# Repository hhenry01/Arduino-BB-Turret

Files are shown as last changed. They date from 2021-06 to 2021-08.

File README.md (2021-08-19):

# Arduino-BB-Turret
## About
The BB Turret is a project developed for [Zen Maker Lab](https://www.zenmakerlab.com/).

The code found under [BB_Turret](https://github.com/hhenry01/Arduino-BB-Turret/blob/main/BB_Turret/BB_Turret.ino) controls the shooting and aiming functions of the turret.

## How it Works
Full details surrounding the project belong to Zen Maker Lab. This README only describes the code and the circuit.
### Shooting

When a button is pressed, the Arduino outputs two voltages to the L298N module in order to spin a motor. One of the input pins is set to *HIGH* while the other is set to *LOW*. For more information, see an [L298N schematic](https://www.handsontec.com/dataspecs/L298N%20Motor%20Driver.pdf).\
\
The motor spins a gear in a rack and pinion system. The gear pushes the rack against a spring. The gear does not have teeth around its entire circumference, so the rack is eventually released and is propelled forward by a spring, hitting and shooting a projectile.

### Aiming
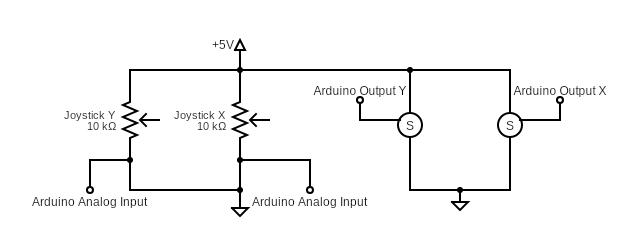
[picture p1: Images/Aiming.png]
Aiming Circuit


To aim the turret, a joystick controls the two servo motors. Since servos need specific angles, inputs must be processed. Smooth motion is created by taking the input and resizing it within an acceptable range for speed. Within that range lies different degrees of speed, simulating analog output, which is more intuitive and allows for finer control.\
\
The button in a joystick is not used because a dedicated button is preferable to control the DC motor. Using the joystick button makes it difficult to keep steady and hard to press when holding a direction. With a dedicated button, one can comfortably shoot the turret no matter the situation.\
\
Finally, at the end of the loop, a 10 ms delay is necessary. Without it, any input via the analog stick would cause immediately rotate the servos to their limits.

#### Full Circuit Schematic and Board
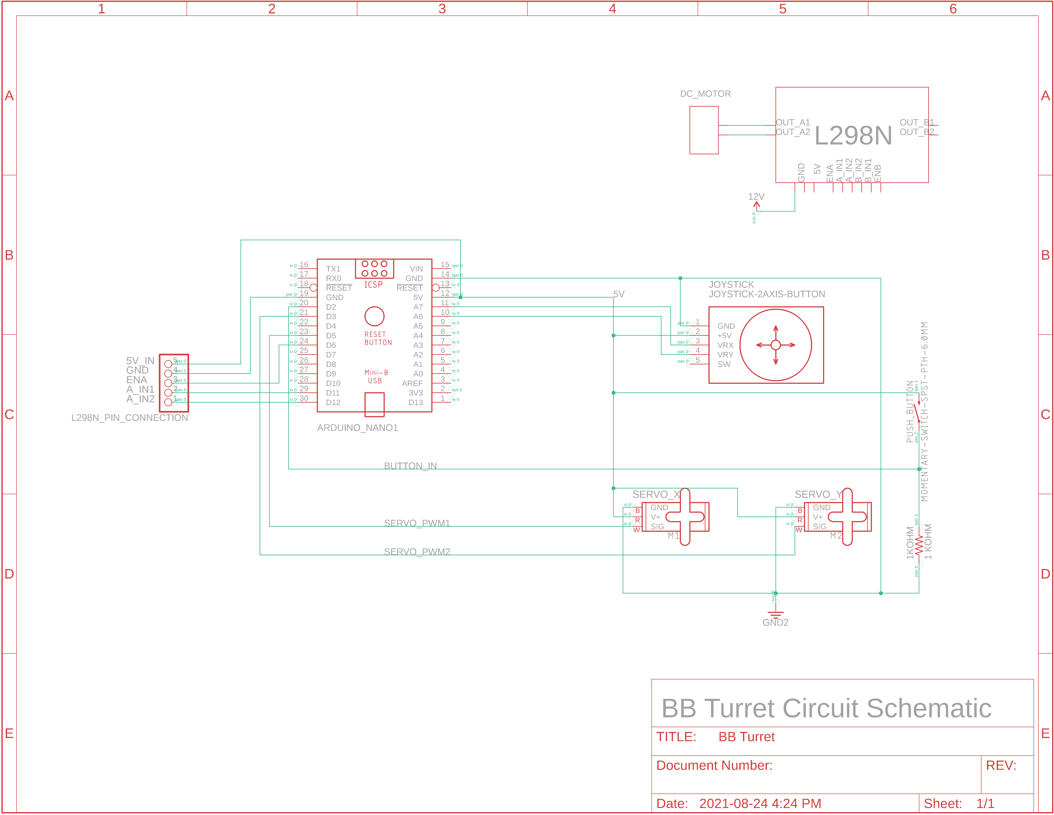
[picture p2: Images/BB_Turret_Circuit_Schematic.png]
Circuit Schematic
\
\
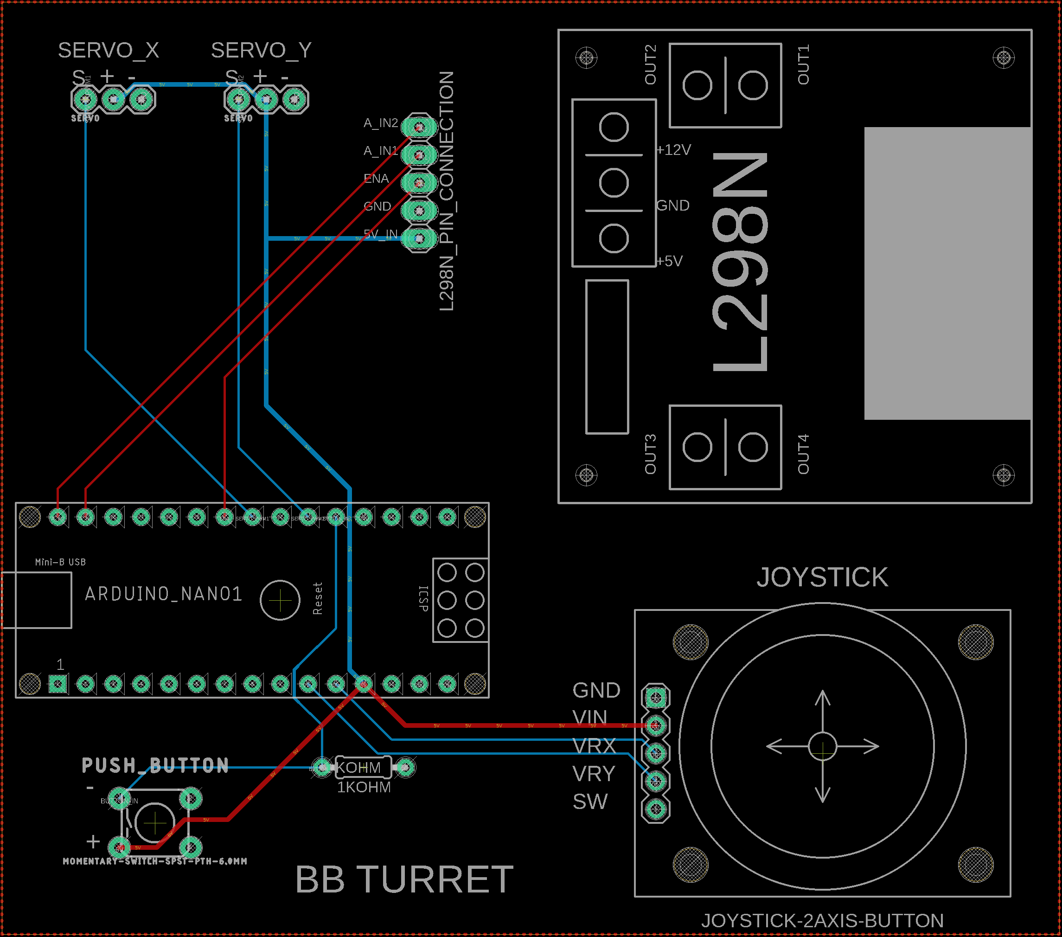
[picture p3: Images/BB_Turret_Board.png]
Board PCB
\
The PCB has a ground plane that connects all ground pins to each other.

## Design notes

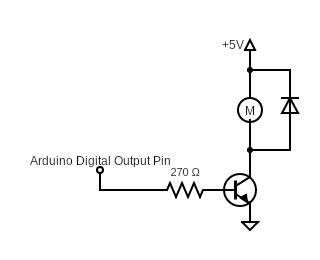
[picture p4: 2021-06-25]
Images/Motor.png

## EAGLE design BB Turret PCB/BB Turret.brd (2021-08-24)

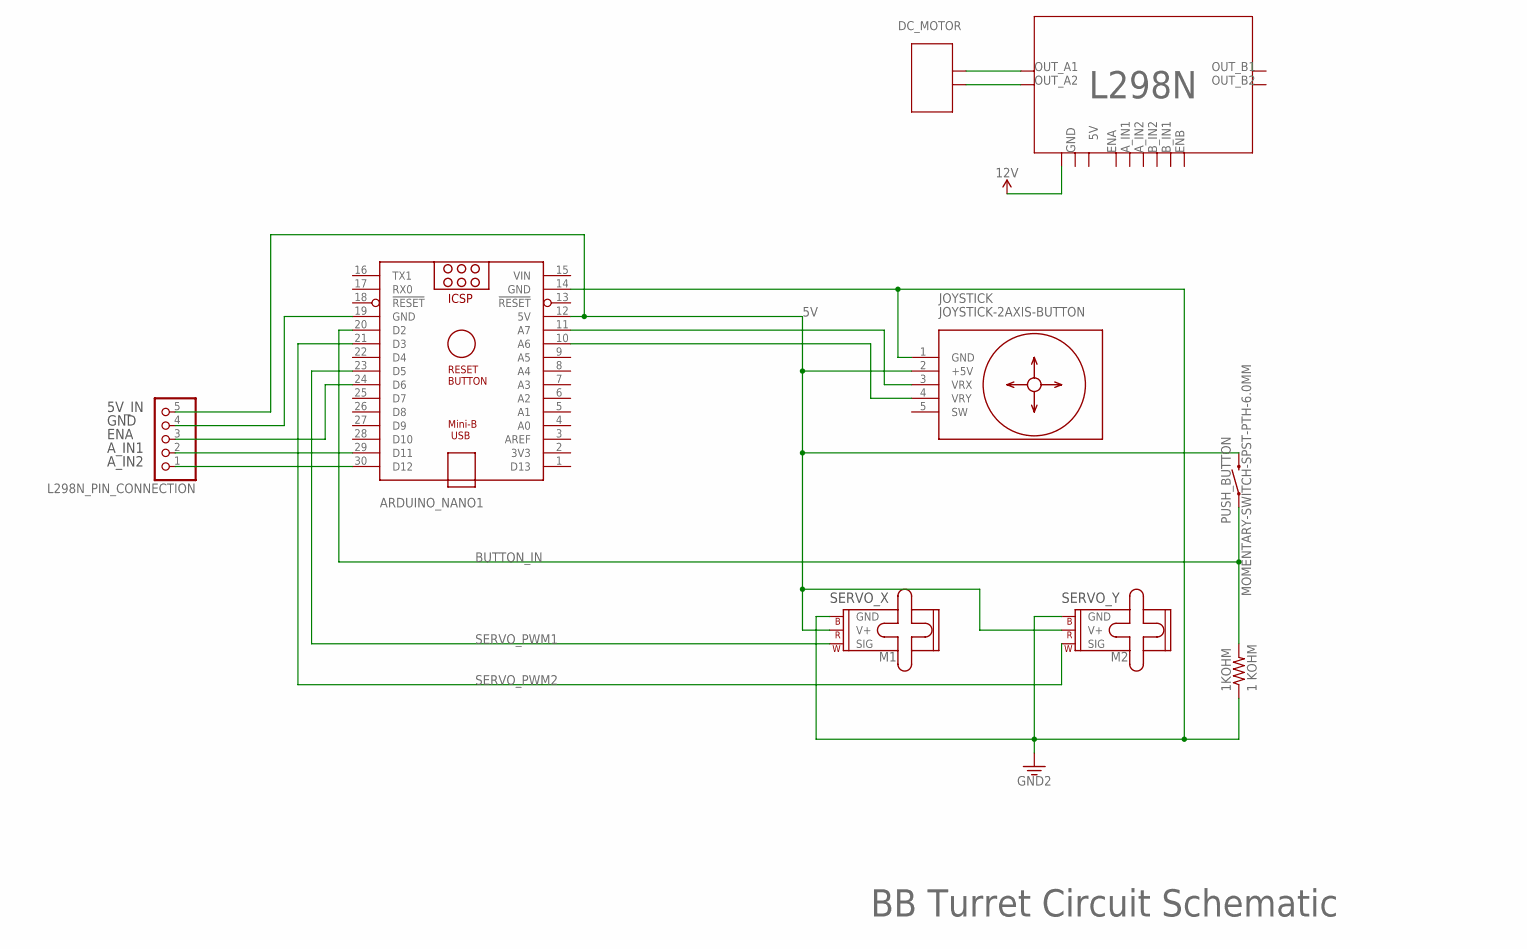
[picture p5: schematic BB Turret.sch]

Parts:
1KOHM: 1 KOHM; 0204/7
ARDUINO_NANO1: ARDUINO_NANO
JOYSTICK: JOYSTICK-2AXIS-BUTTON
L298N_PIN_CONNECTION: PINHD-1X5; 1X05
M1, M2: SERVO; 1X03
PUSH_BUTTON: MOMENTARY-SWITCH-SPST-PTH-6.0MM; TACTILE_SWITCH_PTH_6.0MM

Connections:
5V: ARDUINO_NANO1.12 (5V), JOYSTICK.2 (+5V), L298N_PIN_CONNECTION.5, M1.2 (V+), M2.2 (V+), PUSH_BUTTON.3 (2)
A_IN1: ARDUINO_NANO1.29 (D11), L298N_PIN_CONNECTION.2
A_IN2: ARDUINO_NANO1.30 (D12), L298N_PIN_CONNECTION.1
BUTTON_IN: 1KOHM.2, ARDUINO_NANO1.20 (D2), PUSH_BUTTON.1
ENA: ARDUINO_NANO1.24 (D6), L298N_PIN_CONNECTION.3
GND: 1KOHM.1, ARDUINO_NANO1.14 (GND), ARDUINO_NANO1.19 (GND), JOYSTICK.1 (GND), L298N_PIN_CONNECTION.4, M1.3 (GND), M2.3 (GND)
SERVO_PWM1: ARDUINO_NANO1.23 (D5), M1.1 (SIG)
SERVO_PWM2: ARDUINO_NANO1.21 (D3), M2.1 (SIG)
VIN: ARDUINO_NANO1.15 (VIN)
VRX: ARDUINO_NANO1.11 (A7), JOYSTICK.3 (VRX)
VRY: ARDUINO_NANO1.10 (A6), JOYSTICK.4 (VRY)

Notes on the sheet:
BB Turret Circuit Schematic
L298N
GND
OUT_A1
OUT_A2
ENA
A_IN1
A_IN2
B_IN2
B_IN1
ENB
OUT_B1
OUT_B2
DC_MOTOR
5V_IN
SERVO_X
SERVO_Y

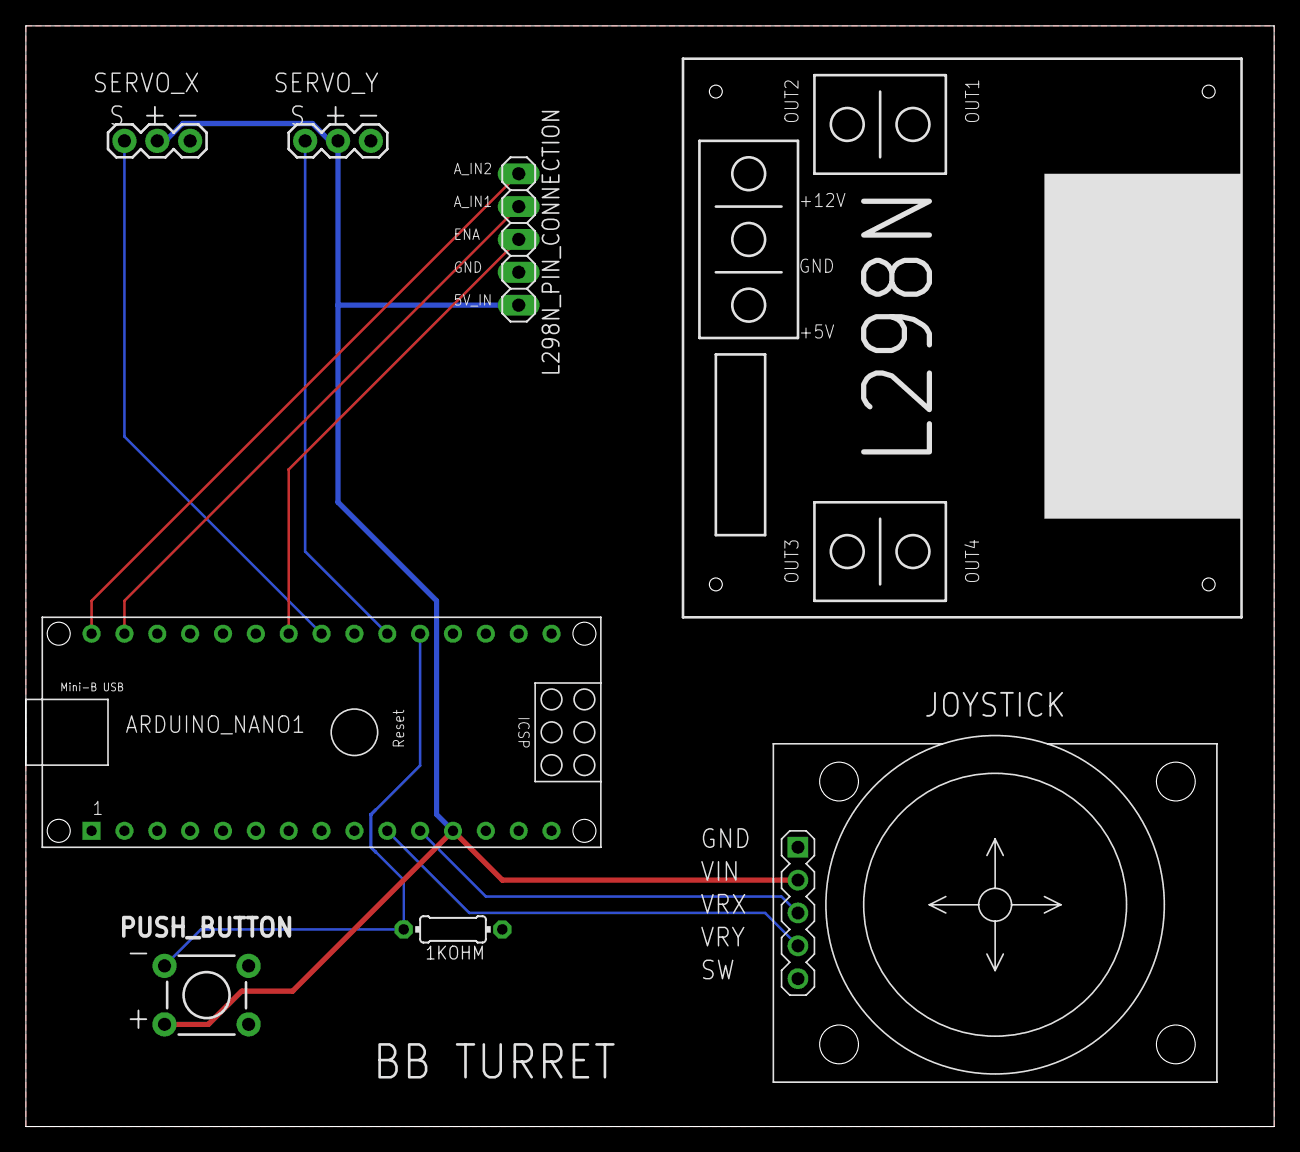
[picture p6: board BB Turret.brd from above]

Board: 2 copper layers, 96.5 x 85.1 mm, 7 parts (0 on the bottom side), 10 nets.

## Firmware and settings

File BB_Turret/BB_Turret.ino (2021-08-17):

#include <Servo.h>
#define FIRE_SPEED 112 // Adjust this value to determine shooting speed.
#define MOTOR_ENABLE 6
#define MOTOR_CONTROL_1 11
#define MOTOR_CONTROL_2 12
#define BUTTON 2
#define JOY_X A7
#define JOY_Y A6
#define SERVO_X 5
#define SERVO_Y 3
#define DEFAULT_ANGLE 90
#define INPUT_RANGE 1023
#define X_MAX 180
#define X_MIN 0
#define Y_MAX 140
#define Y_MIN 60

static const int input_mapping[] = {-3, -2, -1, 0, 1, 2, 3}; //Change for different speed options
static int inputMapSize;
static double inputMapModifier;
int x_angle = DEFAULT_ANGLE;
int y_angle = DEFAULT_ANGLE;
Servo servoX;
Servo servoY;

void setup() {
  Serial.begin(9600);
  pinMode(MOTOR_ENABLE, OUTPUT);
  pinMode(BUTTON, INPUT);
  servoX.attach(SERVO_X);
  servoY.attach(SERVO_Y);
  servoX.write(DEFAULT_ANGLE);
  servoY.write(DEFAULT_ANGLE);
  inputMapSize = sizeof(input_mapping) / sizeof(*input_mapping);
  inputMapModifier = (double) inputMapSize / (double) (INPUT_RANGE-1);
}

void loop() {
  if (digitalRead(BUTTON) == HIGH) {
   analogWrite(MOTOR_ENABLE, FIRE_SPEED); // 
   digitalWrite(MOTOR_CONTROL_1, HIGH);
   digitalWrite(MOTOR_CONTROL_2, LOW);
  } else {
   analogWrite(MOTOR_ENABLE, 0);
   digitalWrite(MOTOR_CONTROL_1, LOW);
   digitalWrite(MOTOR_CONTROL_2, LOW);
  }
  int xVal = analogRead(JOY_X);
  int yVal = analogRead(JOY_Y);
  xVal *= inputMapModifier;
  xVal = min(xVal, inputMapSize-1); //min is necessary to fit xVal within the range of the inputMap array, else it will access an out of bounds index
  yVal *= inputMapModifier;
  yVal = min(yVal, inputMapSize-1);
  xVal = input_mapping[xVal];
  yVal = input_mapping[yVal];
  x_angle += xVal;
  y_angle += yVal;

  // The servos cannot go past their maximum ranges, but a limit needs to be set in the code to avoid it increasing indefinitely
  if (x_angle > X_MAX) x_angle = X_MAX;
  else if (x_angle < X_MIN) x_angle = X_MIN;
  
  if (y_angle > Y_MAX) y_angle = Y_MAX;
  else if (y_angle < Y_MIN) y_angle = Y_MIN;
  
  servoX.write(x_angle);
  servoY.write(y_angle);
  delay(10); // Delay to slow down overall speed. Modify to adjust overall speed.
}

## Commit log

2021-06-03 Added simple motor control on button press.
2021-06-25 Added Circuit Diagrams.
2021-06-26 Added full schematic, updated README.
2021-08-16 Switched schematic image for one with a higher resolution.
    [BB Turret.brd, BB Turret.sch]
2021-08-17 Modified BB_Turret.ino so that it uses the correct PWM pins on the Arduino. Need to update images and PCB.
    [BB_Turret.ino]
2021-08-17 Minor change to code. Added TODO.txt for current issues and potential fixes.
    [BB_Turret.ino]
2021-08-18 Changes listed in TODO.txt didn't work out. May need changes that are too complex. Current iteration is functional.
2021-08-19 Updated PCB files to be up to date with the code and current breadboard circuit. Updated images and README.
    [BB Turret.brd, BB Turret.sch]
2021-08-19 Added missing line regarding ground plane in README.
2021-08-24 Fixed circuit and PCB so that the Arduino does not need USB power.
    [BB Turret.brd, BB Turret.sch]

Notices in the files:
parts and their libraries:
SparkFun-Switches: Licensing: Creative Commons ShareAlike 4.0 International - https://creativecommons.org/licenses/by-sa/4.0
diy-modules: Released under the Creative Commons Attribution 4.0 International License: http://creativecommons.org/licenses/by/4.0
